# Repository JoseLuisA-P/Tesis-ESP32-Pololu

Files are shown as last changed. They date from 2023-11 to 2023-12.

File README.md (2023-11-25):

# Desarrollo de una placa de expansión para los agentes Pololu 3Pi+ que expanda sus capacidades dentro del ecosistema Robotat.

Este trabajo se desarrolló con el objetivo de ampliar las capacidades de los agentes 3Pi+ utilizados en la plataforma de pruebas Robotat. Para aumentar las capacidades del agente, se implementó un manipulador serial de 3 grados de libertad, el cual utiliza servomotores como actuadores y contiene un efector final tipo garra. También, se implementó una cámara OpenMV Cam H7 que permite capturar desde el punto del agente un fotograma o una serie de fotogramas, para realizar un livestream del agente mientras realiza otras rutinas o capturar una imagen en un punto clave de la ejecución de una rutina. Por último, se implementó un algoritmo para el estacionamiento automático del agente, el cual permite el retorno del agente a una posición establecida mientras evita los obstáculos en la plataforma, lo que permite automatizar el proceso de pruebas y asegurar un correcto funcionamiento del agente. Estas expansiones y el agente son controlados desde un TinyS3, el cual dota al agente y sus módulos con la capacidad de ser controlado por medio de una conexión WiFi, desde un cliente remoto con la capacidad de expandirse a múltiples lenguajes al utilizar instrucciones sencillas para su control.

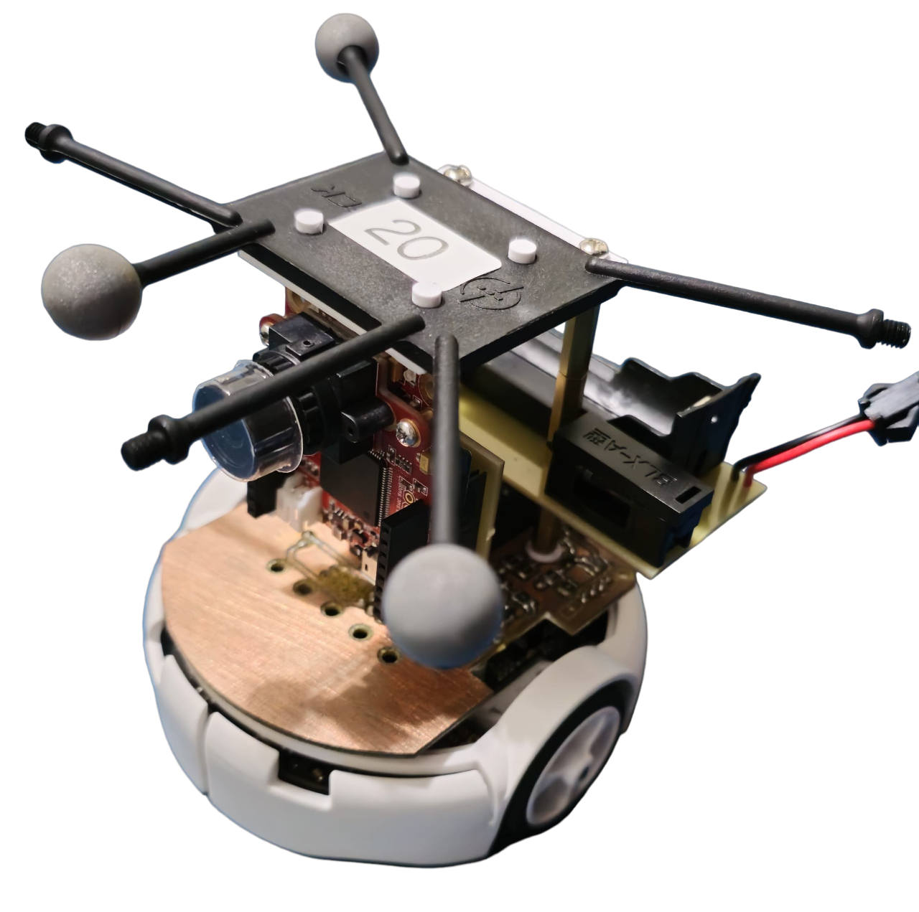
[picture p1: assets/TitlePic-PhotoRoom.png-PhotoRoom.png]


Que contiene este repositorio:
- El firmware utilizado por la placa TinyS3.
- Los códigos para el control del agente y módulos desde Python.
- Manual para el ensamble de las placas de expansion y los modulos.
- Videos de las pruebas para el correcto ensamblaje del agente.
- Enlaces a las pruebas y validación del agente.

### Tabla de contenido:
- [Plataforma de trabajo](#Plataforma-de-trabajo)
- [Estructura del repositorio](#Estructura-del-repositorio)
- [Como ensamblar los modulos y placas](#Como-ensamblar-los-modulos-y-placas)
- [Resultados](#Resultados)

### Plataforma de trabajo

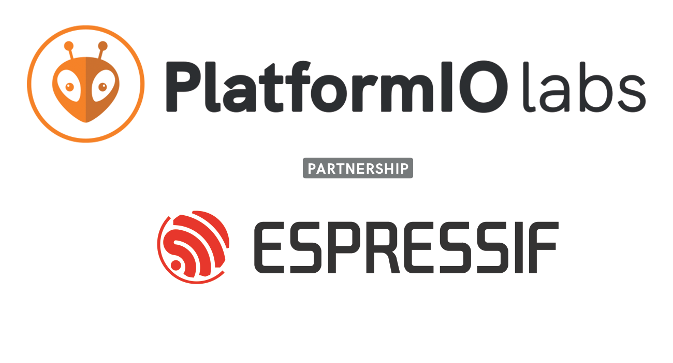
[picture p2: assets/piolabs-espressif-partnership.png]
Platformio y ESPRESSIF


El firmware del agente se desarrolló utilizando la plataforma PlatformIO en VSCode, junto con el framework de ESP-IDF desarrollado como una extensión por ESPRESSIF. La elección de VSCode para este proyecto se debe a su alta flexibilidad para configurar el entorno de desarrollo, desde las alertas visuales hasta el manejo de errores y las diversas extensiones para interactuar con módulos y bibliotecas. Además, su fácil integración con GitHub y la gestión de versiones permitieron un desarrollo más eficiente.

Se utilizó la extensión de PlatformIO debido a las diversas herramientas que contiene para programar y preparar los entornos de trabajo para diversas placas y microcontroladores. Esta extensión permite crear proyectos específicos para cada placa, configurar sus características de manera sencilla, seleccionar las versiones del lenguaje a utilizar y manejar los errores de compilación. En el lado físico, permite programar las placas desde VSCode, utilizar el monitor serial para leer los mensajes de error y configurar acorde al puerto y velocidad de comunicación con la placa. Además, facilita compilar el proyecto y verificar los errores al cargar datos a las placas.

El framework de ESP-IDF se eligió principalmente por la fácil integración de FreeRTOS, lo que permite aprovechar al máximo las capacidades de la placa y optimizar su rendimiento multitarea. Además, este framework permite utilizar las bibliotecas desarrolladas por ESPRESSIF para un manejo eficiente de los módulos de las placas basadas en ESP32, proporcionando mayor flexibilidad en su configuración y permitiendo el uso del multiplexado de los pines para los distintos módulos.

Altium Designer

Para el desarrollo de las PCBs, se utilizó Altium Designer 2021. Aunque este software permite el uso de librerías de objetos comunes, fue necesario agregar librerías personalizadas para cada uno de los componentes adquiridos localmente sin un modelo definido. La elección de Altium Designer se debe a la variedad de herramientas que ofrece para el desarrollo de PCBs y la facilidad para modificar e interconectar proyectos.

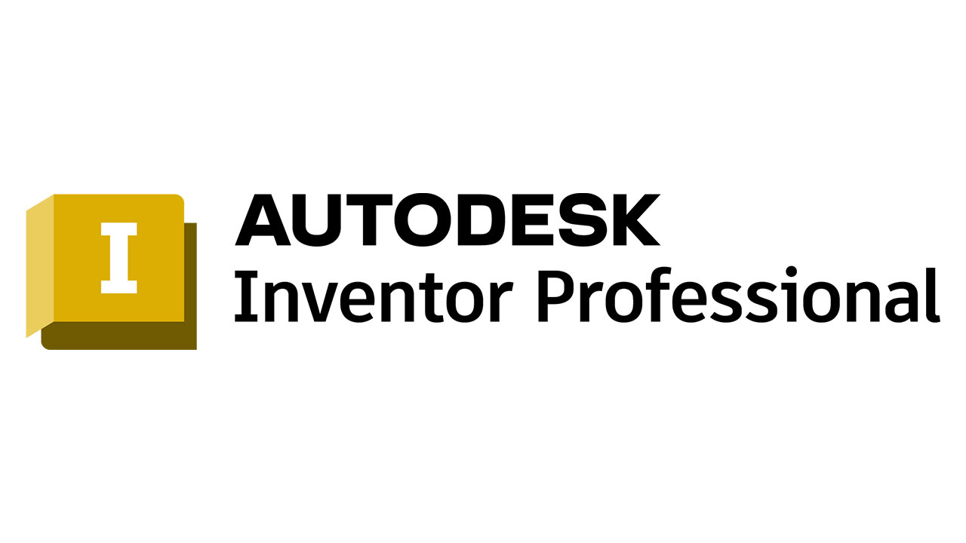
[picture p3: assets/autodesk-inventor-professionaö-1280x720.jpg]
Inventor


En cuanto al diseño de elementos físicos, se llevó a cabo en Autodesk Inventor 2024. Al contar con una interfaz robusta e intuitiva para el diseño y aprovechando la licencia profesional proporcionada por la universidad, es una herramienta que he utilizado a lo largo de mi carrera. Esta elección permitió minimizar el tiempo de desarrollo gracias a la familiaridad con la herramienta.

### Estructura del repositorio

El repositorio se encuentra estructurado de la siguiente forma:
- En la carpeta [**PruebasCOMS**](/PruebasCOMS), se encuentra el proyecto utilizado para configurar y crear el firmware del TinyS3.
- En la carpeta [**assets**](/assets) se encuentran las imágenes utilizadas para este repositorio.
- En la carpeta [**Videos**](/Videos) se encuentran videos de las pruebas de ensamblaje de este trabajo.
- En la carpeta [**Manufactura**](/Manufactura) se encuentran los archivos para manufacturar las PCBs e imprimir las piezas de este trabajo.
- En la carpeta [**ControlCliente**](/ControlCliente) se encuentran los scripts para el control del agente desde Python.
- En la carpeta [**Camara**](/Camara) se encuentra el script para el envio bajo demanda de la imagen desde la OpenMV Cam H7.

### Como ensamblar los modulos y placas

Para ensamblar los módulos y placas utilizados en este trabajo, puede hacer referencia al documento **"ManualDeEnsamble.pdf"**. En este documento, encontrará una breve descripción de las placas, así como instrucciones detalladas sobre cómo ensamblar las placas y módulos. Además, se proporciona información sobre cómo montarlos y detalles sobre otros materiales adicionales que podrían ser necesarios en el proceso.

En el proceso de ensamblaje, se incluyen referencias a pruebas creadas para observar el correcto funcionamiento del agente antes de desplegarlo, lo que facilita el diagnóstico durante su ensamblaje.

### Resultados

En este archivo se incluye un listado de enlaces a videos de YouTube sin listar, en estos se puede observar el comportamiento del agente y las diversas pruebas realizadas. Las pruebas realizadas incluyen tanto los modulos de manera individual como la integracion de los multiples modulos operando al mismo tiempo.

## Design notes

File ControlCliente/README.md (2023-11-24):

## Tabla de contenido:
- [Contenido de esta carpeta](#Contenido)
- [Requerimientos del sistema](#Sistema)
- [Clase para controlar el agente](#funciones)
- [Compatibilidad con otros lenguajes](#Compatibilidad)

## Contenido de esta carpeta

En esta carpeta se encuentra un conjunto de scripts creados para controlar el agente mediante una conexión WiFi.

En el archivo "FuncionesControlPololu.py", se ha creado la clase **PololuAgent**. Esta clase permite controlar al agente de manera sencilla mediante métodos que modifican las variables de control del agente y le hacen interactuar con su entorno.

Los archivos que comienzan con "Test_" en su nombre son pruebas realizadas para explorar las capacidades del agente, su tiempo de respuesta y la repetibilidad de sus instrucciones.

Los archivos que comienzan con "Script_" son referenciados en el manual de ensamble y sirven para realizar pruebas durante el ensamble del agente.

Por último, los archivos que comienzan con "Rutina_" se utilizan para inicializar o probar una configuración en el agente, colocándolo en posiciones iniciales o condiciones de prueba requeridas en su ensamble.

## Requerimientos del sistema

Se requiere de un sistema operativo con Python 3.x y con capacidad de conectarse por WiFi.

## Clase para controlar el agente

La clase para controlar el agente se encuentra en el script "FuncionesControlPololu.py". Esta clase permite controlar al agente y sus módulos de manera simple, sin limitar la profundidad de su control, ya que a los módulos se les pueden enviar valores en bruto para su control.

Para crear el objeto, se requiere la dirección IP del host, en este caso, la dirección de la placa al conectarse, y el puerto que se utilizará para la conexión. Al crear el objeto, se asignan en atributos privados la dirección IP, el puerto utilizado, se crea un buffer interno para el manejo de mensajes, y se crean las variables de odometría y de la batería del agente.

### Descripcion de los metodos
- `connect()`: Crea la conexión con el agente y el socket TCP a utilizar.
- `disconnect()`: Se desconecta del agente, elimina el socket creado y, si es necesario, limpia el buffer.
- `on()`: Envía el carácter de control para encender al agente y sus módulos, además, enciende la bandera para la adquisición de imágenes desde la cámara.
- `off()`: Envía el carácter de control para apagar al agente y sus módulos, y apaga la bandera para la adquisición de imágenes desde la cámara.
- `arm_raw_config()`: Envía el carácter de control para indicar al agente que debe actualizar la configuración del manipulador serial. Junto con el carácter, se envían en grados las configuraciones de las juntas del manipulador.
- `arm_coords()`: Envía el carácter de control para indicar al agente que debe actualizar el manipulador a una coordenada solicitada. Junto con el carácter de control, se envían las coordenadas para posicionar el efector final del manipulador.
- `battery_update()`: Envía el carácter de control para solicitar el nivel de la batería, recibe el dato en bruto obtenido por el ADC del TinyS3 y luego actualiza los atributos privados del voltaje y porcentaje de batería.
- `get_battery_voltage()` y `get_battery_level()`: Retornan como flotante el valor de voltaje o porcentaje de batería obtenidos.
- `set_motor_speed()`: Recibe los valores de velocidad de las ruedas izquierda y derecha como flotantes, los agrega al buffer interno del objeto junto con el carácter de control para indicar que las velocidades se deben actualizar y los envía al agente como un arreglo de bytes.
- `get_image()`: Envía el carácter de control al agente para solicitar la imagen y recibe 4800 bytes que representan el último fotograma guardado por el agente. Los agrega a un arreglo de NumPy y retorna este arreglo.
- `get_odo()`: Envía el carácter de control al agente para la solicitud de la odometría interna y recibe 12 bytes. Luego, convierte estos bytes en flotantes y los agrega a las variables internas del agente.

### Como utilizar esta clase

Previo a utilizar estos scripts es necesario conectarse a la red wifi del agente, 

**Importando la libreria y creando el objeto**
```python
from FuncionesControlPololu import PololuAgent

HOST = "192.168.4.1" #Direccion IP del host, TinyS3
PORT = 3333 #El puerto que se le va asignar al agente

agent1 = PololuAgent(HOST,PORT) #Creando el objeto con las variables
```

Para importar la librería al script que se está modificando en el momento, basta con tener el script "FuncionesControlPololu.py" en la misma carpeta e importar "PololuAgent". Con esta clase importada, se establece la dirección IP para conectarse con el agente y se asigna el puerto deseado, en este caso, se utilizó 3333 por conveniencia. Al establecer la dirección y el puerto, se puede crear el objeto pasando estas variables.

**Como conectarse y encender el agente**
```python
agent1.connect()    #Conectarse al agente
agent1.on()         #Encender al agente y sus módulos.
time.sleep(5)       #Este delay es de seguridad, asegura que todos los sistema se inicialicen correctamente
```

Con el objeto creado, se puede utilizar **connect()** para realizar la conexión con el socket. En caso de fallar la conexión, el manejo de errores al crear el socket detiene la ejecución del código e indica en la terminal el motivo por el cual no se pudo realizar la conexión. Al estar conectado al agente, se puede encender junto con sus módulos con **on()** y luego esperar de 5 a 10 segundos. Este delay es por seguridad y permite que tanto el agente, como la cámara y el manipulador serial terminen de configurarse.

**Como apagar al agente y desconectarse**
```python
agent1.off()            #Apagar al agente y sus módulos.
agent1.disconnect()     #Desconectarse del agente
```

Al terminar la ejecucion del programa se puede apagar al agente con **off()**, esto apaga al agente y sus modulos, luego se puede desconectar con **disconnect()**, lo que libera el socket del agente y permite que este acepta otra conexion a futuro. Previo a apagar el agente se recomienda dejarlo en reposo, velocidades de 0, y el manipulador serial en la posicion de reposo presentada en el manual, esto para asegurar que al encerse no se mueva de manera descontrolada o se arruine el manipulador.

***Las siguientes aplicaciones requieren al agente estar encendido y al cliente conectado a la red***

**Como mover al agente actualizando los valores de velocidades de sus llantas**

```python
#Establecer las velocidades para las llantas
velocidad_izquierda = 10.0
velocidad_derecha = 10.0

agent1.set_motor_speed(velocidad_izquierda,velocidad_derecha) #Enviar estas velocidades al agente para actualizarlas
```

Si se busca mover el agente, se puede enviar directamente la velocidad de cada llanta de manera individual. Para ello, basta con establecer su valor como flotante y luego, con **set_motor_speed()**, colocar estas velocidades. Esto enviará las velocidades al agente y actualizará su valor. Estas velocidades también pueden ser calculadas por un algoritmo de control, como un PID, y luego, pasar el resultado de la iteración al método para actualizar al agente.

**Como mover el manipulador serial**
```python
#Configuracion en grados de cada una de las juntas del manipulador
junta_1 = 90
junta_2 = 90
efector = 180

#Pasar estos valores al metodo para actualizar la configuracion en el agente
agent1.arm_raw_config(junta_1,junta_2,efector)
```

Para mover el manipulador con mayor precisión o después de utilizar un algoritmo de cinemática inversa, se puede utilizar **arm_raw_config()**. Este método recibe la configuración de cada junta en grados y la envía al agente para actualizar físicamente el manipulador.

```python
#Coordenadas para mover el efector final
coordenadaX = 50
coordenadaY = 50

#Enviar las coordenadas para posicionar el manipulador
agent1.arm_coords(coordenadaX,coordenadaY)
```

Para mover el efector final del manipulador a una posición coordenada específica, se utiliza **arm_coords()**. Este método recibe las coordenadas para mover el efector y actualiza su configuración internamente.

**Obtener la informacion de la celda**

```python
agent1.battery_update() #actualiza el valor de la bateria al ultimo leido por el agente

print(agent1.get_battery_voltage())     #Imprime el voltaje de la bateria
print(agent1.get_battery_level())       #Imprime el porcentaje restante de carga de la bateria
```

Si se requiere saber el nivel de batería del agente, primero se deben actualizar los atributos del objeto con **battery_update()**. Este método solicita al agente el último valor leído de la celda y lo envía al cliente. Con este valor actualizado, se puede obtener el voltaje de la celda con **get_battery_voltage()** o el porcentaje de carga restante con **get_battery_level()**. Al retornar un valor los últimos dos métodos, se pueden utilizar para actualizar una variable de control.

**Obtener informacion de la odometria interna del agente**

```python
agent1.get_odo()        #Obtener la odometria del agente
agent1.odoX             #Acceder a la coordenada X de la odometria
agent1.odoY             #Acceder a la coordenada Y de la odometria
agent1.odoTheta         #Acceder al ángulo Theta de la odometria
```

Para obtener la configuración del agente por medio de odometría interna, se puede utilizar **get_odo()**. Este método solicita el valor actualizado de odometría del agente y lo envía al cliente. Al haber actualizado la odometría del agente en el objeto, se puede acceder a sus valores utilizando **.odoX**, **.odoY** o **.odoTheta**. Las coordenadas están en metros y el ángulo está en radianes.

**Obtener el ultimo fotograma desde el agente y graficarlo con Matplolib**
```python
raw_image = agent1.get_image()                  #Obtener el fotograma como un vector fila de bytes
processed_image = raw_image.reshape(60,80)      #Cambiar sus dimensiones por una matriz de 60X80
fg = plt.figure()                               #Crear la figura
ax = fg.gca()                                   #Crear el objeto para los ejes
fg.show()                                       #Mostrar la figura
h = ax.imshow(processed_image, cmap = 'gray')   #Actualizar el valor de la figura con el arreglo y colocarlo en blanco y negro
plt.show()                                      #Mostrar la imagen
```

Para obtener el último fotograma obtenido con la cámara, se puede utilizar **get_image()**. Este método solicitará al agente el último fotograma obtenido y lo enviará al cliente como un vector fila de bytes. Luego, con este valor en bruto, se puede redimensionar con NumPy, crear una figura y graficarlo con Matplotlib para visualizar lo que ve el agente.

```python
#Se utiliza para temporizar la toma de fotogramas
actual_time = time.time()
n = 0
capture = 0

#Durante 20 segundos se toma video de lo que ve el agente y se imprime en pantalla
while(n < 200):
    elapsed_time = time.time()
    diff = elapsed_time - actual_time
    
    if(elapsed_time > 0.1):
        capture = 1
        n = n + 1
        
    if(capture):
        raw_image = agent1.get_image()
        if(len(raw_image) >= 4700):
            processed_image = raw_image.reshape(60,80)
            h.set_data(processed_image)
            draw(), pause(0.05)
            capture = 0
        else:
            agent1.disconnect()
            time.sleep(0.1)
            agent1.connect()
            
plt.close()
```

En caso se requiera hacer un stream de la imagen desde el agente, se puede emplear el código previo. Este solicita la imagen y al recibir correctamente el fotograma, actualiza la imagen a una tasa de 10 FPS. En caso de fallar, se desconecta del agente para limpiar el buffer y luego solicitar de nuevo la imagen.

***Si se necesita utilizar multiples acciones del agente en conjunto, en los scripts incluidos en esta carpeta se pueden ver multiples ejemplos***

## Compatibilidad con otros lenguajes

Dado que esta clase se escribió utilizando la menor cantidad de librerías en Python, utiliza estructuras para la conversión entre bytes y tipos de datos, y utiliza sockets para conectarse con el agente. Virtualmente, se puede migrar a otros lenguajes que tengan estas funcionalidades con baja dificultad, siempre conservando la baja latencia.

Entre los lenguajes recomendados para su migración están:
- Matlab
- Java
- C++

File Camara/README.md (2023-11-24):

El script presentado en esta carpeta contiene la configuración requerida para el envío bajo demanda de los fotogramas capturados por la cámara. La configuración de la cámara y resolución se pueden modificar acorde a los requerimientos del proyecto para procesar la información necesaria. Se pueden agregar más eventos en el bucle while para que la cámara sea capaz de procesar datos, disminuir la carga en el agente, o realizar un análisis de la imagen y enviar los datos.

Para poder enviar los datos, se debe utilizar la siguiente estructura:

```python
if(handshake.value() == 0):
    envio = sensor.snapshot()
    cs_pin.low()
    interface.send(envio)
    cs_pin.high()
```

En esta condición if, se envía el fotograma al agente. Para que esto suceda, el fotograma debe estar en blanco y negro con una resolución de 60x80 bytes. Si se desea enviar otros datos por SPI desde la cámara, se puede modificar este bucle if y enviar la estructura de datos requerida. Sin embargo, esto requiere modificar la función **AskForPicture()** en el firmware del TinyS3 para que reciba el mensaje del tamaño solicitado y lo procese acorde a lo requerido.

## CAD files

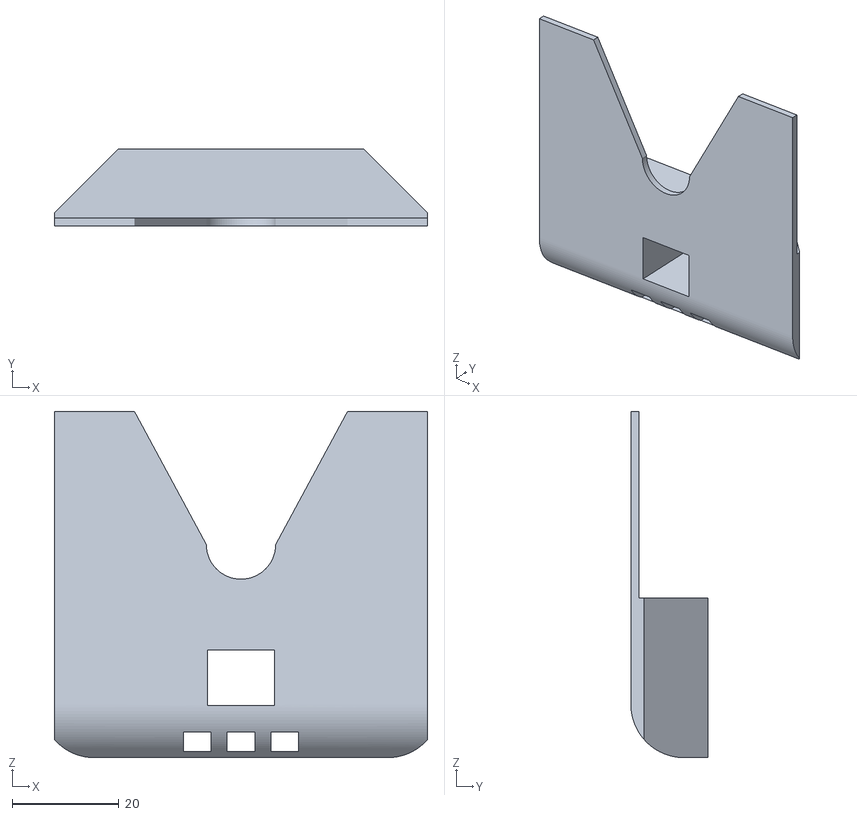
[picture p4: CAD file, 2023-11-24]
Manufactura/Estacion de carga/CharginStationV2.stl
70.0 x 14.5 x 65.0

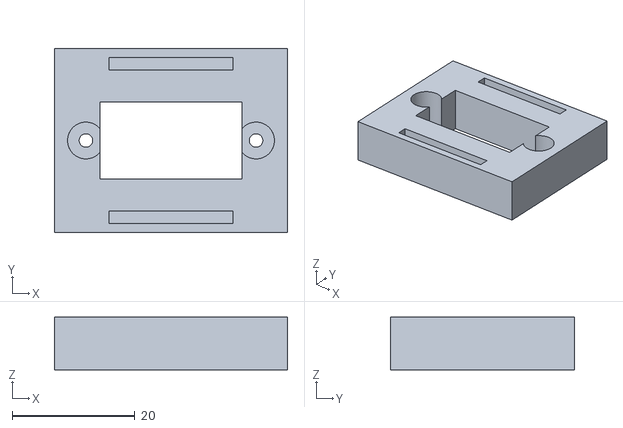
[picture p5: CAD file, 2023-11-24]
Manufactura/Manipulador Serial/BaseGarra-02.stl
38.0 x 30.0 x 8.60

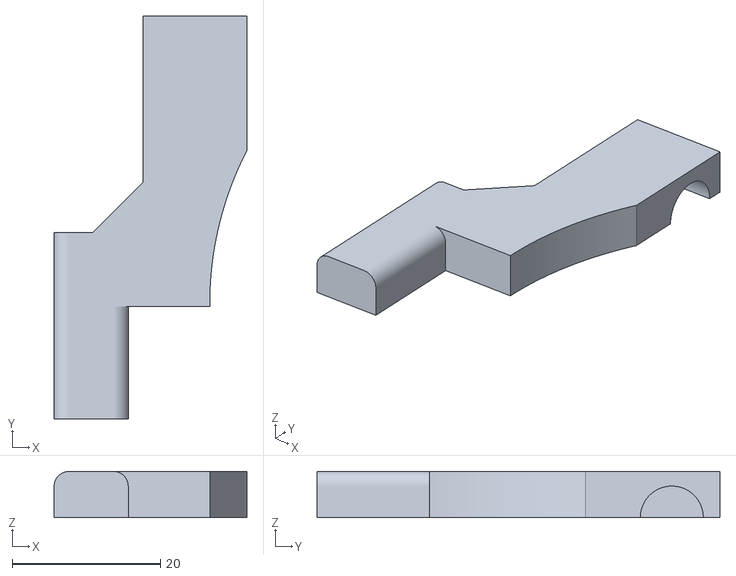
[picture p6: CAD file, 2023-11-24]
Manufactura/Estacion de carga/SoporteCableV2.stl
26.0 x 54.4 x 6.22

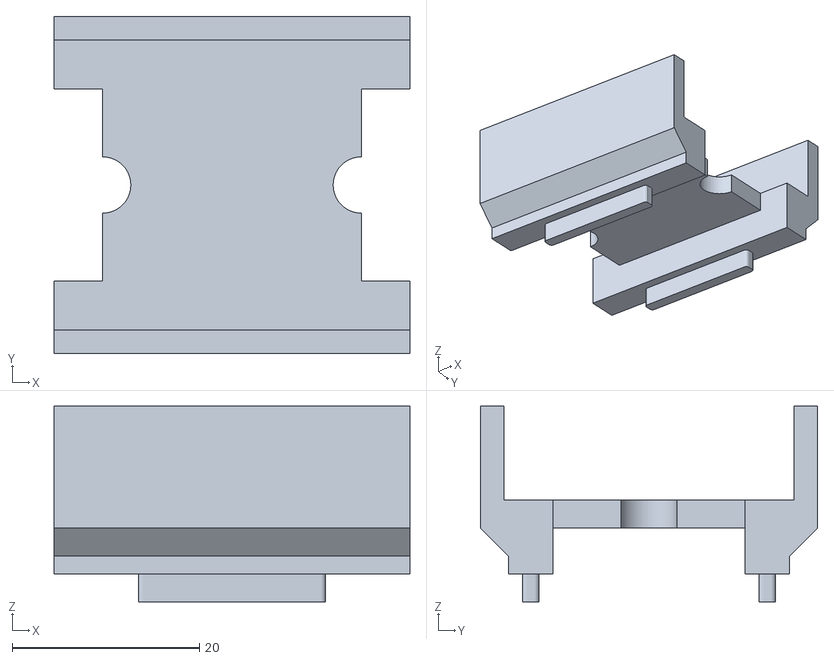
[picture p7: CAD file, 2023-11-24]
Manufactura/Manipulador Serial/BaseGarra-01.stl
38.0 x 36.0 x 20.9

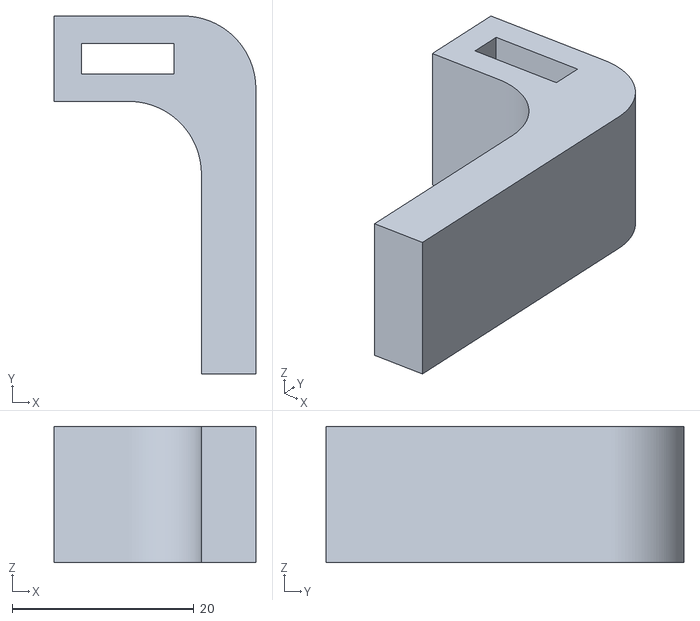
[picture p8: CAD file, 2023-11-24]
Manufactura/Estacion de carga/HolderBarraHubX4.stl
22.2 x 39.4 x 15.0

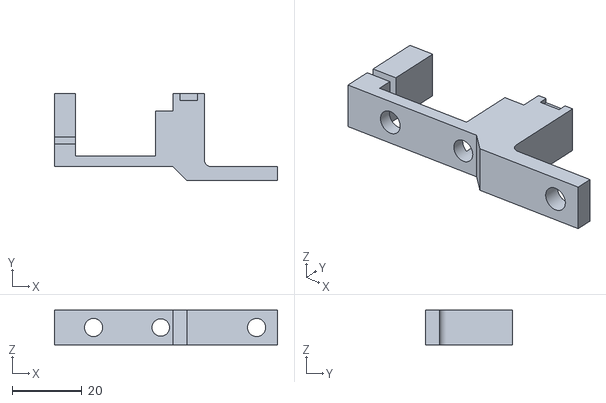
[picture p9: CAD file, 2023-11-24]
Manufactura/Manipulador Serial/Eslabon1-02.stl
64.0 x 25.0 x 10.0

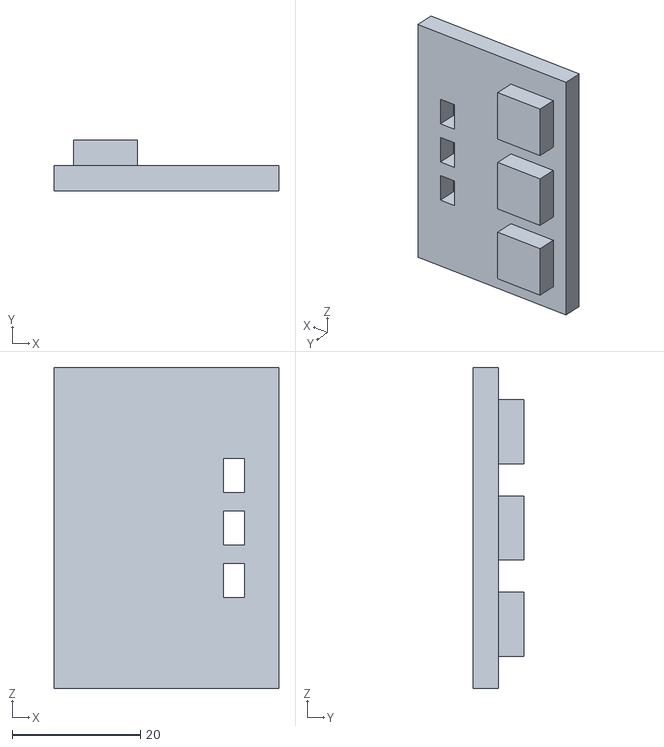
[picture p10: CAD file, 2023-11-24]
Manufactura/Estacion de carga/HolderChargerX3.stl
35.0 x 8.00 x 50.0

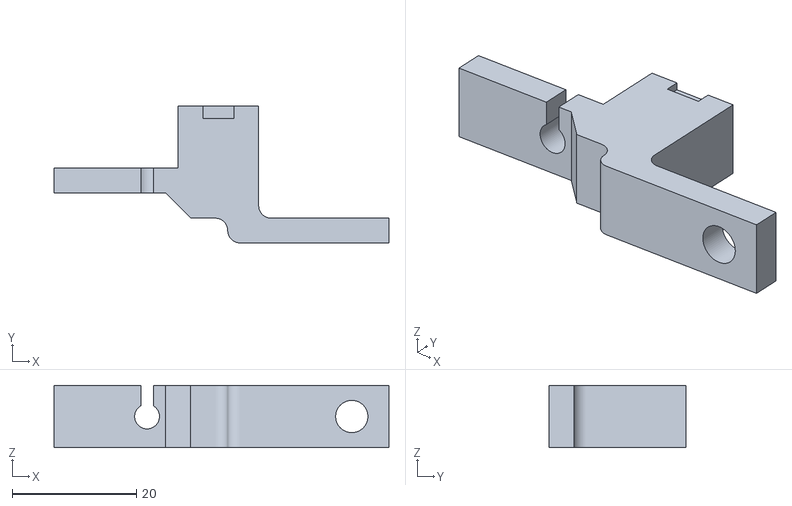
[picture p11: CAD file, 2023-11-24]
Manufactura/Manipulador Serial/Eslabon2-02.stl
54.0 x 22.1 x 10.0

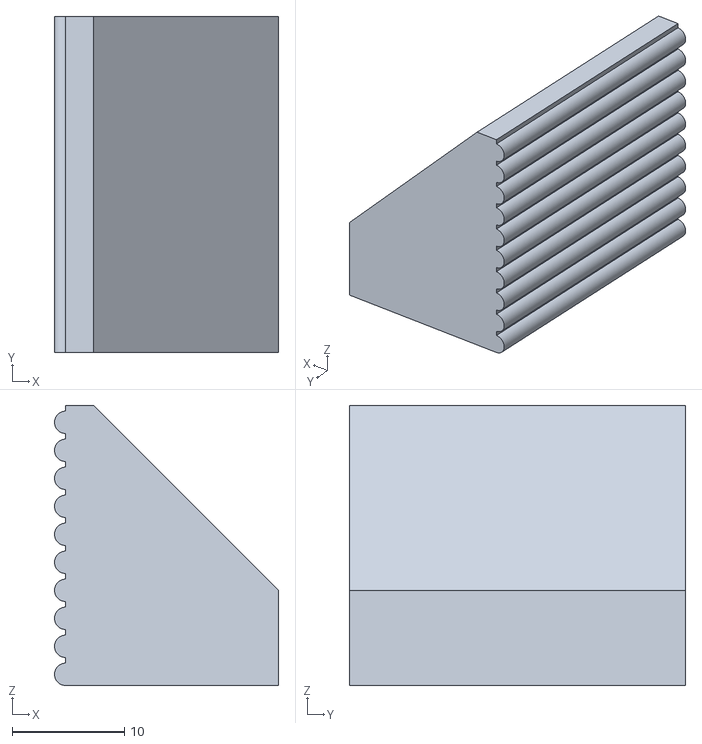
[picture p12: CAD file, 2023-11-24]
Manufactura/Manipulador Serial/GarraManoX2.stl
20.0 x 30.0 x 25.0

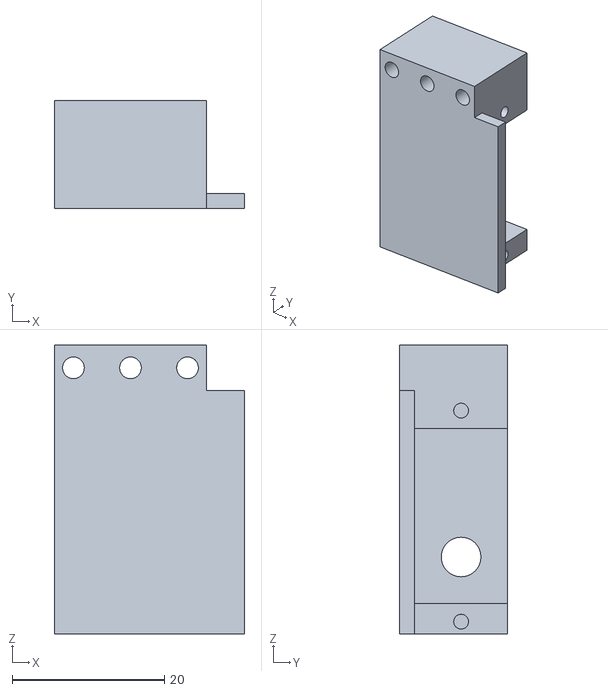
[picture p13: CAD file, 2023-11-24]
Manufactura/Manipulador Serial/BaseBrazoV1.stl
25.0 x 14.2 x 38.0

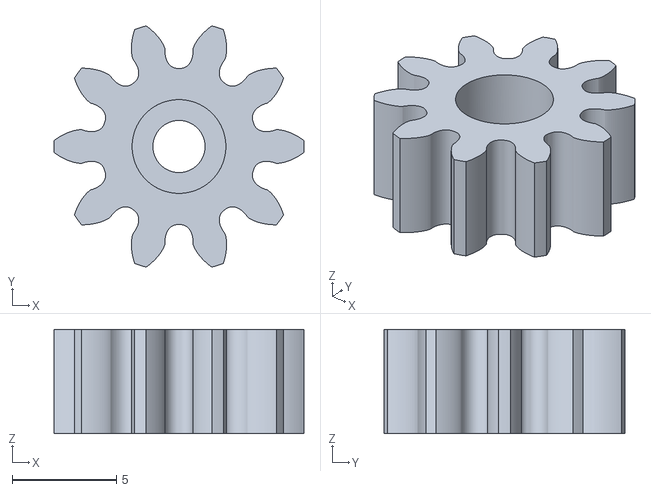
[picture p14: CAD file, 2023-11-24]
Manufactura/Manipulador Serial/EngraneServoX2.stl
12.0 x 11.6 x 5.00

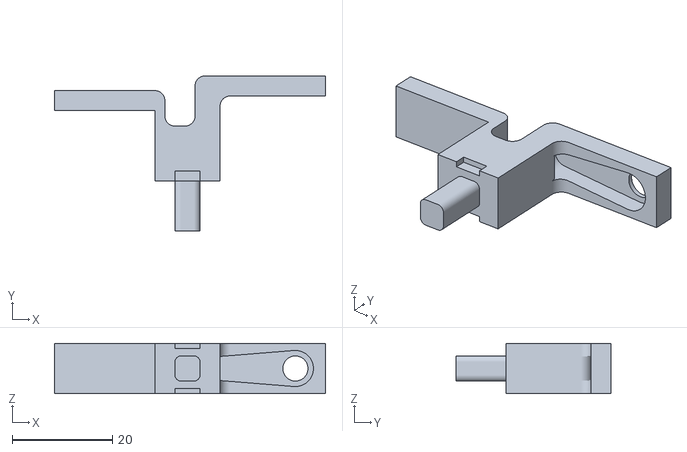
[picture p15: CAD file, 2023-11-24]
Manufactura/Manipulador Serial/Eslabon2-01.stl
54.0 x 30.9 x 10.0

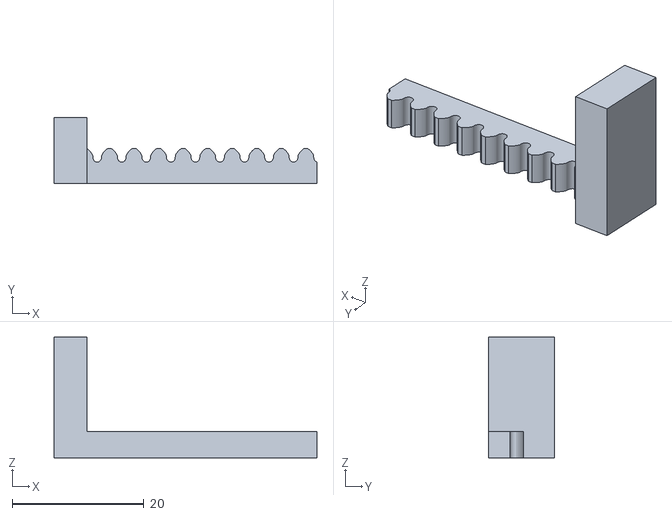
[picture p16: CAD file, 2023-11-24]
Manufactura/Manipulador Serial/BrazoGarraX2.stl
40.0 x 10.0 x 18.4

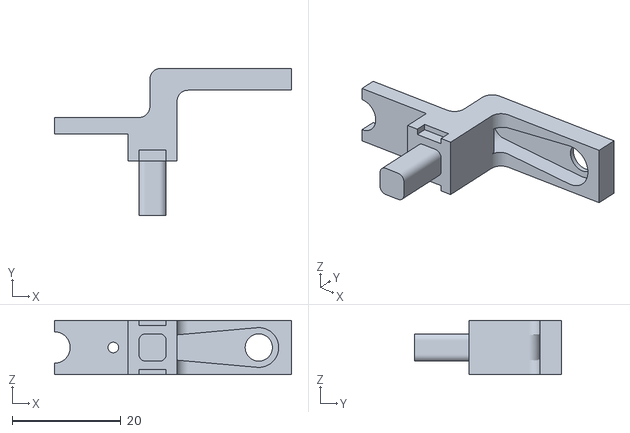
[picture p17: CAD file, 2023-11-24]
Manufactura/Manipulador Serial/Eslabon1-01.stl
43.5 x 27.0 x 10.0

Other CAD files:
Manufactura/Estacion de carga/SoporteCableV2P2.stl

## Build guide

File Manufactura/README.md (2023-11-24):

# En cada carpeta se encuentran los archivos STL o planos de corte para fabricar las piezas del agente. 
## Estos están listos para ser enviados al MakerLab y así proceder con la manufactura.

En algunos de los archivos STL adjuntos, al final de su nombre, se encuentra un sufijo "XN", donde N es la cantidad de piezas a imprimir. Esta cantidad corresponde a generar una instancia del modelo para ensamblar un componente completo. Además, sigue la nomenclatura del MakerLab para asegurar que se generen los elementos adecuados. 
En esta carpeta no se incluyen los archivos de documentación de las piezas, que indican el orden de impresión, dimensiones o cantidad a imprimir, ya que esta información puede variar sin previo aviso por parte del MakerLab.

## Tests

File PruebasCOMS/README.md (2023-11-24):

## Tabla de contenido:
- [Acerca de este proyecto](#Acerca-de-este-proyecto)
- [Requerimientos del proyecto](#Requerimientos-del-proyecto)
- [Preparando el entorno](#Preparando-el-entorno)
- [Configuracion de la placa](#Configuracion-de-la-placa)
- [Breve descripcion de las funciones](#Breve-descripcion-de-las-funciones)

## Acerca de este proyecto
Este proyecto se creó para el desarrollo del firmware a utilizar en el TinyS3, el cual es el módulo central de control del agente robótico. Este dota al agente de la capacidad de comunicarse con clientes a través de WiFi, utilizando una lógica simple para el envío y recepción de datos. Además, esta placa permite controlar los módulos del manipulador serial y la cámara montada en el agente, tanto de manera individual como en paralelo, al fijar el envío de instrucciones en un orden específico que se presenta posteriormente.

Se desarrolló con el framework de ESP-IDF para el uso de las librerías creadas por ESPRESSIF para las placas basadas en el chip ESP32. Además, se utilizó para integrar FreeRTOS en el proyecto y mejorar el rendimiento del agente en actividades multitarea.

En este contexto, FreeRTOS dota al agente con un pseudo sistema operativo, el cual permite al agente responder a instrucciones enviadas desde un cliente, actualizar sus variables de control y actualizar el estado de sus módulos, con muy baja latencia. Esto es ideal para agentes robóticos en plataformas de desarrollo y estudio, ya que amplía la posibilidad de implementarlo en algoritmos de enjambre.

## Requerimientos del proyecto

Este proyecto puede ser modificado en Windows, MacOS o cualquier distribución de Linux capaz de ejecutar VSCode y PlatformIO. Además, el equipo debe ser capaz de ejecutar Python 3.x y Matlab R2021a en adelante. Estos requisitos son necesarios para poder ejecutar las funciones del cliente, interactuar con el robotat y tener la capacidad de modificar el proyecto.

## Preparando el entorno

Para instalar VSCode, se puede seguir el siguiente [enlace](https://code.visualstudio.com/docs/setup/setup-overview). Este enlace proporciona una visión general de VSCode, y se debe de seleccionar el sistema operativo que se esta utilizando. Se recomienda tener GitHub instalado e integrarlo en el entorno de VSCode, lo que facilitará, en el futuro, la actualización de la información del proyecto al contar con un punto de retorno seguro y comprobado, ademas de un eficiente manejo de versiones.

Una vez que se ha instalado VSCode en el sistema, es necesario instalar la extensión de PlatformIO, lo cual se puede realizar siguiendo las instrucciones del siguiente [enlace](https://platformio.org/install/ide?install=vscode).

Con la extensión de PlatformIO instalada, se debe de descargar este proyecto en su última versión para modificarlo, realizar un fork o clonarlo en un repositorio personal. Teniendo el proyecto disponible en tu equipo, puedes importarlo haciendo clic en **Open project** o **Abrir proyecto** en la página de inicio de PlatformIO.

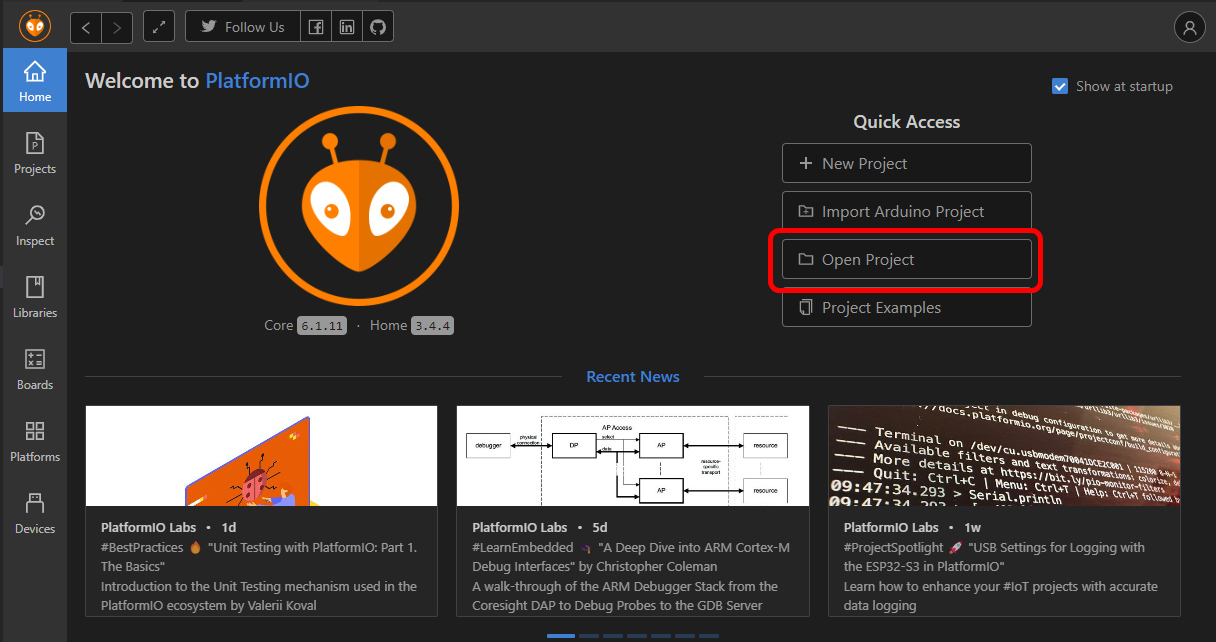
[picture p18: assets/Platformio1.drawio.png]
Importar el proyecto


Al hacer clic en este acceso rápido, se selecciona la carpeta donde se descargó el proyecto y, luego, se debe de hacer clic en abrir. Este proceso descargará las librerías requeridas por el proyecto, actualizará las librerías existentes y descargará los scripts necesarios para programar la placa. Este proceso suele tomar entre 5 y 25 minutos, y es importante que la computadora no entre en reposo durante este tiempo. Sin embargo, no es necesario mantener la aplicación abierta, por lo que se puede realizar otras actividades mientras se importa el proyecto.

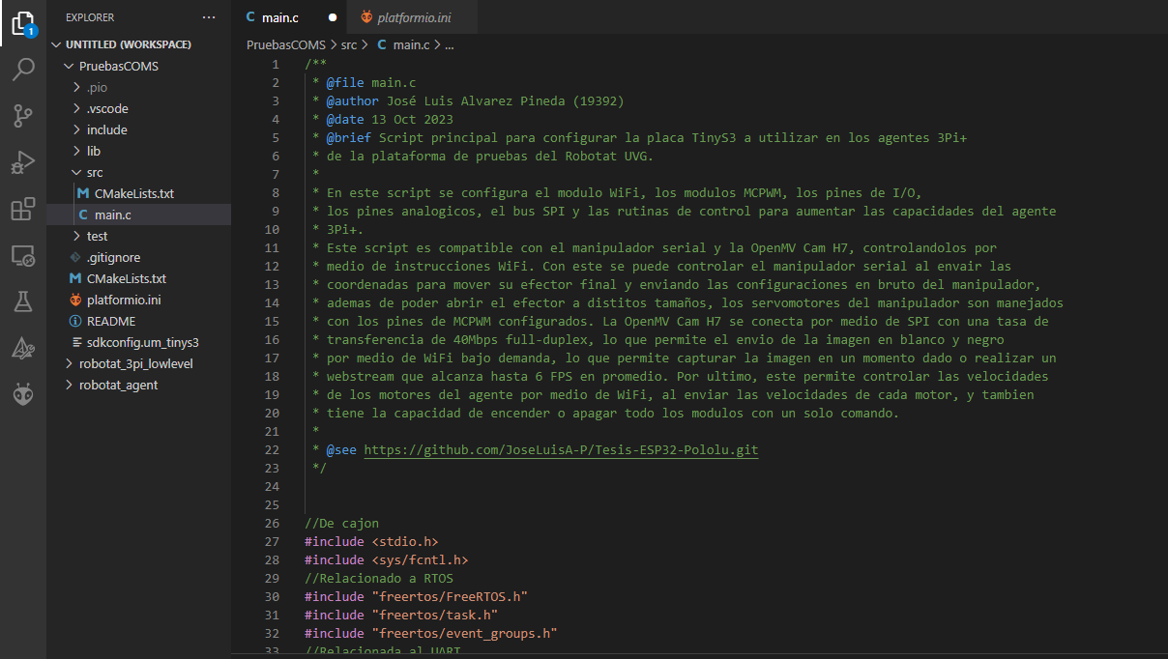
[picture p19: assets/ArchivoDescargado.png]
Como se ve el proyecto importado


Al finalizar la importación del proyecto, se agregará al workspace actualmente abierto o a un workspace sin nombre, como se muestra a la izquierda. Dentro de él, en la carpeta "src", encontrarás el archivo principal (main.c) del proyecto. Al abrirlo, verás la pantalla como se muestra en la imagen superior. Después de dar clic en compilar, se generará una versión lista para cargar en la placa y comenzar a trabajar. Con esto completado, el proyecto se ha importado correctamente y está listo para ser modificado.

En caso de que surjan errores durante la compilación o la importación, las advertencias de PlatformIO son explícitas y permiten resolver los errores al leerlos de manera adecuada. Si, después de seguir las indicaciones de PlatformIO, no puedes importar el proyecto, se recomienda descargarlo e instalarlo en el escritorio de tu equipo.

## Configuracion de la placa

Para configurar la placa al iniciar un proyecto nuevo o importar porciones del proyecto, se puede utilizar la siguiente configuración:

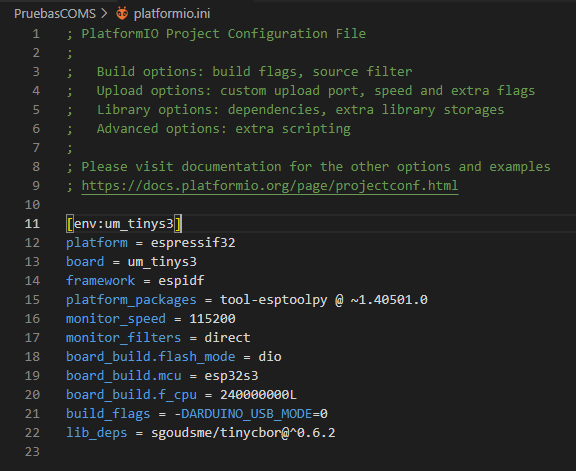
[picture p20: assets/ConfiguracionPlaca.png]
Configuraion de la placa


La configuración presentada es capaz de ejecutar todas las librerías utilizadas y aprovechar al máximo las capacidades de la placa. Además, permite la lectura de distintos tipos de mensajes de la placa y los diferencia por color, haciendo más intuitivo el proceso de pruebas y desarrollo.

# Breve descripcion de las funciones
Las funciones utilizadas para configurar este proyecto se pueden separar en grupos, cada uno encargado de configurar un módulo y agregar propiedades para realizar tareas específicas.

**Configuración del Módulo WiFi:**
- `wifi_init_softap()`: Inicializa y configura el módulo WiFi como punto de acceso (AP).
- `nvs_init()`: Inicializa el sistema de almacenamiento no volátil y lo actualiza a la versión más actual al cargar el firmware.
- `wifi_event_handler()`: Se encarga de manejar los eventos que se llevan a cabo en la red WiFi, además, imprime los eventos para facilitar las pruebas.

**Configuración del Socket TCP:**
- `tcp_socket_init()`: Inicializa el socket TCP y crea la tarea del handler para manejar los mensajes y solicitudes del cliente.
- `handle_socket()`: Maneja los datos recibidos por el cliente y realiza acciones después de leer la variable de control.

**Comunicación con el Agente a través del Bus UART:**
- `UART_init()`: Configura el bus UART con los parámetros requeridos por el agente.
- `uart_tx()` y `uart_rx()`: Encargadas del envío y recepción periódico de datos al agente utilizando el bus UART.
- `decodeCBOR()`: Decodifica el contenedor de CBOR recibido en el bus y asigna los valores en este a las variables de odometría interna.
- `encodeCBOR()`: Codifica las velocidades de las ruedas del agente, agregándolas a un contenedor de CBOR.

**Comunicación con la Cámara a través del Bus SPI:**
- `SPI_init_config()`: Configura el módulo SPI, asigna los callbacks para las transmisiones y activa el pin de handshake.
- `my_pre_cb()` y `my_post_cb()`: Son los callbacks de la transmisión SPI y cambian el estado del pin de handshake para solicitar información a la cámara.
- `AskForPicture()`: Bucle que solicita bajo demanda la imagen desde la cámara y actualiza el buffer de la última imagen capturada.

**Manipulador Serial utilizando el Módulo MCPWM:**
- `mcpwm_initialize()`: Configura e inicializa los 3 canales de PWM.
- `updatePositionSCH()`: Actualiza los ciclos de trabajo de los canales de PWM de cada servomotor ante modificaciones realizadas por el cliente.
- `CalcConfig()`: Calcula la configuración y ciclo de trabajo requerido por los servomotores para colocarlos en una coordenada especificada por el cliente.

**Lectura de la Celda para la Alimentación del Agente:**
- `ADCConfig()`: Configura e inicializa el canal ADC en modo oneshot.
- `BatteryUpdate()`: Realiza lecturas periódicas al nivel de la batería y almacena el último valor leído en una variable.

Dado que el código utiliza envíos de datos al cliente bajo demanda y parte de estos datos son recabados de manera periódica al encender el agente, se utiliza `initSemaphores()` para inicializar y configurar las estructuras de control.

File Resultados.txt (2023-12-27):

Enlace a la lista de odometria: https://www.youtube.com/playlist?list=PLaFg6usfbdtRm5OenLyibr4apW4UIxrPD

Enlace a la lista del manipulador serial: https://www.youtube.com/playlist?list=PLaFg6usfbdtTwx68LOk1SOFYHa42CXAxg

Enlace a la lista del livestream: https://www.youtube.com/playlist?list=PLaFg6usfbdtTZ6Gpa1hlmyx4xLoYTJxLw

Enlace a la lista de odometria y livestream: https://www.youtube.com/playlist?list=PLaFg6usfbdtQjJjsxPqYbJ4kCr4Ms4ZXF

Enlace a la lista de odometria y manipulador serial: https://www.youtube.com/playlist?list=PLaFg6usfbdtSEN4Z2sSBTVOfirNpEE59O

Enlace a la lista de pruebas del manual:https://www.youtube.com/playlist?list=PLaFg6usfbdtSpVdTMnJFs3VnT3rEh2SlV

Enlace a la lista de parqueo del agente: https://www.youtube.com/playlist?list=PLaFg6usfbdtT4JosoJN846-d9nKsDRila

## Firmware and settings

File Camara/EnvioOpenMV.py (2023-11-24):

import sensor, image, pyb
from pyb import SPI

RED_LED_PIN = 1

sensor.reset()
sensor.set_pixformat(sensor.GRAYSCALE)
sensor.set_framesize(sensor.QQQVGA)

handshake = pyb.Pin('P4',pyb.Pin.IN)
pyb.LED(RED_LED_PIN).on()
sensor.skip_frames(time=1000)

interface = pyb.SPI(2, SPI.MASTER,baudrate=40*1000*1000, polarity = 0, phase = 0)
cs_pin = pyb.Pin("P3",pyb.Pin.OUT_PP) #Es necesario activar el pin manualmente

comprate = 10

#envio = sensor.snapshot().compressed(comprate).bytearray()
envio = sensor.snapshot()
print(envio.size())
#print(len(envio))

while(1):
    pyb.LED(RED_LED_PIN).off()
    if(handshake.value() == 0):
        #pyb.LED(RED_LED_PIN).on()
        #envio = sensor.snapshot().compressed(comprate).bytearray()
        envio = sensor.snapshot()
        #print(len(envio))
        cs_pin.low()
        interface.send(envio)
        cs_pin.high()
        #print("Enviado")

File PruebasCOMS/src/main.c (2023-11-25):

/**
 * @file main.c
 * @author José Luis Alvarez Pineda (19392)
 * @date 13 Oct 2023
 * @brief Script principal para configurar la placa TinyS3 a utilizar en los agentes 3Pi+
 * de la plataforma de pruebas del Robotat UVG.
 *
 * En este script se configura el modulo WiFi, los modulos MCPWM, los pines de I/O,
 * los pines analogicos, el bus SPI y las rutinas de control para aumentar las capacidades del agente
 * 3Pi+.  
 * Este script es compatible con el manipulador serial y la OpenMV Cam H7, controlandolos por 
 * medio de instrucciones WiFi. Con este se puede controlar el manipulador serial al envair las 
 * coordenadas para mover su efector final y enviando las configuraciones en bruto del manipulador,
 * ademas de poder abrir el efector a distitos tamaños, los servomotores del manipulador son manejados 
 * con los pines de MCPWM configurados. La OpenMV Cam H7 se conecta por medio de SPI con una tasa de 
 * transferencia de 40Mbps full-duplex, lo que permite el envio de la imagen en blanco y negro 
 * por medio de WiFi bajo demanda, lo que permite capturar la imagen en un momento dado o realizar un
 * webstream que alcanza hasta 6 FPS en promedio. Por ultimo, este permite controlar las velocidades
 * de los motores del agente por medio de WiFi, al enviar las velocidades de cada motor, y tambien 
 * tiene la capacidad de encender o apagar todo los modulos con un solo comando.
 * 
 * @see https://github.com/JoseLuisA-P/Tesis-ESP32-Pololu.git
 */


//De cajon
#include <stdio.h>
#include <sys/fcntl.h>
//Relacionado a RTOS
#include "freertos/FreeRTOS.h"
#include "freertos/task.h"
#include "freertos/event_groups.h"
//Relacionada al UART
#include "driver/uart.h"
#include "driver/gpio.h"
#include "sdkconfig.h"
//Relacionado al Wifi
#include "esp_mac.h"
#include "esp_wifi.h"
#include "esp_event.h"
#include "esp_log.h"
#include "nvs_flash.h"
#include "lwip/err.h"
#include "lwip/sys.h"
//Implementando el stack TCP-IP
#include "esp_system.h"
#include "esp_netif.h"
#include "lwip/sockets.h"
#include <lwip/netdb.h>
//Manejo de Strings
#include <string.h>
//Manejo de los servos
#include "driver/ledc.h"
#include "driver/mcpwm.h"
#include "soc/mcpwm_reg.h"
#include "soc/mcpwm_struct.h"
//Relacionado al SPI
#include "driver/spi_slave.h"
#include "driver/spi_master.h"
//Codificando con CBOR
#include "../src/cbor.h"
//Operaciones trigonometrica
#include <math.h>
//Lectura con el ADC
#include "esp_adc/adc_oneshot.h"
#include "esp_adc/adc_cali.h"
#include "esp_adc/adc_cali_scheme.h"

//Variables para pruebas y cambio de placa

#define isTinyS3
//#define testeo

//Parametros para la configuracion del servidor
#define SSID                "Pololu3Pi+"
#define WIFIPASSWORD        "MT30062023"
#define WIFICHANNEL         2
#define MAXCONNECTIONS      1

//Puerto para la comunicacion
#define PORT 3333
int sock;
int LisSock;
uint8_t tcpavail = 0;
uint8_t odometry_request = 0;
uint8_t battery_request = 0;

//Parametros para configurar el timer del LEDC
#define LEDC_TIMER              LEDC_TIMER_0
#define LEDC_MODE               LEDC_LOW_SPEED_MODE
#define LEDC_DUTY_RES           LEDC_TIMER_10_BIT // Resolucion del ciclo de trabajo de 13 bits

//Parametros para configurar el canal y pin del servo con el LEDC
#define SERVO1_CHANNEL          LEDC_CHANNEL_0
#define SERVO1_PIN              GPIO_NUM_1
#define SERVO2_CHANNEL          LEDC_CHANNEL_1
#define SERVO2_PIN              GPIO_NUM_2
#define SERVO3_CHANNEL          LEDC_CHANNEL_2
#define SERVO3_PIN              GPIO_NUM_3

//Parametros para calcular el duty en base al angulo
const uint32_t minDeg = 0;
const uint32_t maxDeg = 180;
const uint32_t minDuty = 500;
const uint32_t maxDuty = 1000;
uint32_t dutyValue;

//Configuracion de pines para el SPI
#define SPI_NAME    SPI2_HOST
#define SPI_MISO    GPIO_NUM_37
#define SPI_MOSI    GPIO_NUM_35
#define SPI_CLK     GPIO_NUM_36
#define SPI_CS      GPIO_NUM_34
#define SPI_HAND    GPIO_NUM_9

//PIN para encender el pololu
#define POLOLUSWITCH    GPIO_NUM_4

//Variables para las solicitudes
#define BUFFER_SIZE 4800                // Tamaño del Buffer para la recepcion de datos
char rx_buffer[BUFFER_SIZE];            // Buffer para los datos recibidos por SPI
uint8_t SPIAsk = 0;                     // Bandera de control para la solicitud de datos
spi_device_interface_config_t CamH7;    // Configuracion de la camara como dispositivo conectado por SPI
spi_device_handle_t  SPIHandle;         // Handle para el modulo SPI configurado

static const char *TAG = "Prueba"; //TAG para el log de errores o informacion

#define SERVO_MIN_PULSEWIDTH 400  // Pulso minimo en microsegundos
#define SERVO_MAX_PULSEWIDTH 2400 // Pulso maximo en microsegundos
#define SERVO_MAX_DEGREE 180      // Angulo maximo para los manipuladores

#define CBOR_BUF_SIZE       (32)    //Tamaño del mensaje de CBOR
#define CBOR_MSG_MIN_SIZE   (16)    //Tamaño minimo del mensaje de CBOR

uint8_t sendOdo = 0;                                // Para enviar la odometria al cliente
char odo_buffer[BUFFER_SIZE];                       // Buffer para la odometria
float xi_odo[3];                                    // Valores de [x,y,theta] del agente
uint8_t cbor_buf_tx[CBOR_BUF_SIZE] = {0};           // Buffer para la recepcion de datos CBOR
uint8_t cbor_buf_rx[CBOR_BUF_SIZE] = {0};           // Buffer para el envio de datos CBOR
static const unsigned int odoread_time_ms = 100;    // Tiempo de control para la lectura de la odometria
CborEncoder encoder, array_encoder;                 // Variable de encoder y de encoder para un arreglo de datos en CBOR
CborParser parser;                                  // Parser para el arreglo en CBOR
volatile float phi_ell = 0;                         // Variable para la velocidad de la rueda izquierda
volatile float phi_r = 0;                           // Variable para la velocidad de la rueda derecha

union{
    float input_flotante;
    uint8_t bytes[4];
} odoX, odoY, odoTheta; //Para convertir los floats en bytes y luego enviarlos al cliente

float odo_x = 0;                        //Guarda el ultimo valor de X leido por odometria
float odo_y = 0;                        //Guarda el ultimo valor de Y leido por odometria
float odo_theta = 0;                    //Guarda el ultimo valor de Theta leido por odometria
uint8_t odoBuffer[sizeof(float)*3];     //Buffer para la decodificacion de los datos

#define RX_BUF_SIZE         (1024)          //Tamaño maximo del buffer
#define UART_PORT           UART_NUM_2      //Modulo UART utilizado para la comunicacion
#define TXD_PIN             (GPIO_NUM_7)    //Numero de GPIO utilizado para TX
#define RXD_PIN             (GPIO_NUM_8)    //Numero de GPIO utilizado para RX

static const unsigned int control_time_ms = 100; //Tiempo de control, para la transmision de las variables de controla al agente

SemaphoreHandle_t xSemaphore1, xSemaphore2; //Estructura de control para los mensajes

/**
 * \struct
 * @brief Estuctura utilizada para conservar los parametros del manipulador serial.
 *
 * En esta estructura se incluyen los valores de configuracion de las juntas y su 
 * ciclo de trabajo.  Los valores de las juntas es el angulo que deben de mantener
 * acorde a la ultima configuracion realizada, con este valor se realizan los pasos 
 * para calcular el nuevo ciclo de trabajo y asi colocar la junta en esa configuracion,
 * ademas de utilizarse como el ultimo valor configurado.
 * El valor del ciclo de trabajo se utiliza para mantener la posicion luego de 
 * actualizar la configuracion de la junta y colocar el manipulador en su posicion
 * luego de un reinicio.
 * 
 */

typedef struct {
    uint32_t joint1;    /**< Configuracion de la junta 1, en grados. */
    uint32_t joint2;    /**< Configuracion de la junta 2, en grados. */
    uint32_t gripper;   /**< Configuracion de la junta 3, en grados. */
    uint32_t duty_us1;  /**< Ciclo de trabajo en la junta 1. */
    uint32_t duty_us2;  /**< Ciclo de trabajo en la junta 2. */
    uint32_t duty_us3;  /**< Ciclo de trabajo en la junta 3. */
}   ManSer;

ManSer brazo = {60,60,100,0,0,0}; //Inicializando los valores en la estructura

uint32_t configj1,configj2,configj3; //Configuracion en grados de las juntas para su control
uint32_t step1,step2,step3; //Para realizar los pasos en los ajustes de las juntas

uint32_t q1, q2; //Configuraciones calculadas
uint32_t es1 = 47; //Largo eslabon 1
uint32_t es2 = 68; //Largo eslabon 2 
uint8_t coordX,coordY;//Configuraciones en XY para colocar el brazo
uint8_t updateCoords = 0;//Para actualizar la configuracion luego de enviar coordenadas

//Variables para el ADC
static int adc_raw[1][10]; //Valores en bruto del ADC
adc_oneshot_unit_handle_t adc1_handle; //Handler para las interrupciones
int batlevel = 0; //Flag para cuando se lee el nivel de bateria
uint8_t battery_buffer[sizeof(int)]; //Buffer para enviar el valor de la bateria por TCP

//Prototipos para algunas funciones
static void AskForPicture(void *arg);

//Para habilitar el debuggeo de la plataforma
#define testeo

/*!
 \fn size_t encodeCBOR(void)
 @brief Codifica las velocidades de la rueda en formato CBOR en un buffer.

 Inicializa el codificador CBOR con el buffer especificado y su tamaño, luego, se crea
 un array de CBOR con las velocidades de cada motor como un punto flotante. Por ultimo, 
 se cierra el contenedor del array y se devuelve el tamaño del buffer para ser enviado.

*/

size_t encodeCBOR(void)
{
    cbor_encoder_init(&encoder, cbor_buf_tx, sizeof(cbor_buf_tx), 0);
    cbor_encoder_create_array(&encoder, &array_encoder, 2);
    cbor_encode_float(&array_encoder, phi_ell);
    cbor_encode_float(&array_encoder, phi_r);
    cbor_encoder_close_container(&encoder, &array_encoder);

    return cbor_encoder_get_buffer_size(&encoder, cbor_buf_tx);
}

/*!
 \fn void UART_init(void)
 @brief Configura la interfaz UART.

 Configura los parametros del UART como la velocidad de transmision, tamaño del mensaje,
 paridad, bits de parada y el control de flujo entre transacciones. Se asignan los pines
 de TX y RX y se instala el controlador, inicializandolo para que opere en transacciones.
 
 \note El buffer de TX puede o no ser configurado, esto dependera del tamaño del mensaje.

*/

void UART_init(void)
{
    const uart_config_t uart_config = {
        .baud_rate = 115200,
        .data_bits = UART_DATA_8_BITS,
        .parity = UART_PARITY_DISABLE,
        .stop_bits = UART_STOP_BITS_1,
        .flow_ctrl = UART_HW_FLOWCTRL_DISABLE,
        .source_clk = UART_SCLK_APB
    };

    uart_driver_install(UART_PORT , RX_BUF_SIZE, 0, 0, NULL, 0);
    uart_param_config(UART_PORT , &uart_config);
    uart_set_pin(UART_PORT , TXD_PIN, RXD_PIN, UART_PIN_NO_CHANGE, UART_PIN_NO_CHANGE);   
}

/*!
 \fn static void wifi_event_handler(void* arg, esp_event_base_t event_base,int32_t event_id, void* event_data)
 @brief Handler del modulo WiFi.

 Despliega informacion sobre los eventos que ocurren luego de crear configurar el modulo WiFi y el Access Point,
 desplegando la direccion MAC e IP de los clientes al conectarse o desconectarse.
 
 \param event_base Define la variable utilizada para registrar el evento.
 \param event_id En este se indica el id del evento a registrar o si se deben de registrar todos los eventos.
 \param event_data Es la informacion de respuesta generada ante el evento registrado.
 \return En el monitor serial el estado de la conexion. 
 \note Este handler se utiliza en la funcion "esp__event_handler_instance_register", no debe de ser utilizado de
 manera directa en el codigo. 
*/

static void wifi_event_handler(void* arg, esp_event_base_t event_base,int32_t event_id, void* event_data)
{
    switch(event_id)
    {
        case WIFI_EVENT_AP_STACONNECTED:
        {
            wifi_event_ap_staconnected_t* event = (wifi_event_ap_staconnected_t*) event_data;
            ESP_LOGI(TAG, "station "MACSTR" join, AID=%d",MAC2STR(event->mac), event->aid);
            break;   
        }
        case WIFI_EVENT_AP_STADISCONNECTED:
        {
            wifi_event_ap_stadisconnected_t* event = (wifi_event_ap_stadisconnected_t*) event_data;
            ESP_LOGI(TAG, "station "MACSTR" leave, AID=%d",MAC2STR(event->mac), event->aid);
            break;
        }
        default:
            break;

    }
}

/*!
 \fn void wifi_init_softap(void)
 @brief Inicializa y configura el modulo WiFi como Access Point (SoftAP)

 Configura el modulo WiFi como un Access Point utilizando el nombre de red (SSID) y contraseña (WIFIPASSWORD),
 este se configura utilizando el protocolo de seguridad WPA2-PSK, manteniendo a la red segura. Al finalizar
 la configuracion despliega un mensaje con los parametros necesarios para la conexion a la red.
 
 \note Solo se debe de llamar una vez y esto luego de haber inicializado la NVS
 \see void nvs_init(void)

*/

void wifi_init_softap(void)
{
    ESP_ERROR_CHECK(esp_netif_init());
    ESP_ERROR_CHECK(esp_event_loop_create_default());
    esp_netif_create_default_wifi_ap();

    wifi_init_config_t cfg = WIFI_INIT_CONFIG_DEFAULT();
    ESP_ERROR_CHECK(esp_wifi_init(&cfg));

    ESP_ERROR_CHECK(esp_event_handler_instance_register(WIFI_EVENT,ESP_EVENT_ANY_ID,&wifi_event_handler,NULL,NULL));

    wifi_config_t wifi_config = {
        .ap = {
            .ssid = SSID,
            .ssid_len = strlen(SSID),
            .channel = WIFICHANNEL,
            .password = WIFIPASSWORD,
            .max_connection = MAXCONNECTIONS,
            .authmode = WIFI_AUTH_WPA2_PSK,
            .pmf_cfg = {
                    .required = true,
            },
        },
    };

    ESP_ERROR_CHECK(esp_wifi_set_mode(WIFI_MODE_AP));
    ESP_ERROR_CHECK(esp_wifi_set_config(WIFI_IF_AP, &wifi_config));
    ESP_ERROR_CHECK(esp_wifi_start());

    ESP_LOGI(TAG, "wifi_init_softap finished. SSID:%s password:%s channel:%d",SSID, WIFIPASSWORD, WIFICHANNEL);
}

/*!
 \fn void nvs_init(void)
 @brief Inicializa el sistema de almacenamiento flash no volatil (NVS).

 Inicializa el sistema de almacenamiento flash no volatil (NVS), verificando la cantidad de 
 paginas libres en la flash y la ultima version utilizada para su configuracion. Si no hay suficientes
 paginas libres o al momento de cargar el codigo hay una nueva version, borra la flash y la
 configura para poder ser utilizada por otros modulos. Por ultimo, despliega en el monitor serial
 los posibles errores que se presenten al configurarla.

*/

void nvs_init(void)
{
    esp_err_t ret = nvs_flash_init();
    if (ret == ESP_ERR_NVS_NO_FREE_PAGES || ret == ESP_ERR_NVS_NEW_VERSION_FOUND) 
    {
        ESP_ERROR_CHECK(nvs_flash_erase());
        ret = nvs_flash_init();
    }
    ESP_ERROR_CHECK(ret);  
}

/*!
 \fn static void TCPSendRobust(void *arg)
 @brief Envio de datos por medio del Socket TCP.

 Envia un paquete de gran tamaño por medio del socket WiFi al ser activada una bandera, 
 utilizando el tamaño del Buffer como referencia. Envia el paquete por porciones, 
 utilizando el ancho de banda maximo cuando es posible. En caso de presentarse un 
 error durante el envio lo despliega en el monito serial y al terminar el envio 
 exitosamente se baja la bandera.

*/

static void TCPSendRobust(void *arg)
{
    while(1)
    {

        if(tcpavail>0)
        {
            if (xSemaphore1 != NULL && xSemaphoreTake(xSemaphore1, (TickType_t)portMAX_DELAY) == pdTRUE){
                #ifdef testeo
                    printf ("TCPEnviado\n");
                #endif
                int to_write = BUFFER_SIZE;
                int written = 0;

                while (to_write > 0) {
                        written = send(sock, &rx_buffer, to_write, 0);
                    if (written < 0) {
                        #ifdef testeo
                            ESP_LOGE(TAG, "Error occurred during sending: errno %d", errno);
                        #endif
                        tcpavail = 0;
                    }
                    to_write -= written;
                }
                
                tcpavail = 0;
                xSemaphoreGive(xSemaphore1);
            }
        }

        vTaskDelay(10/ portTICK_PERIOD_MS);
    }
}

/*!
 \fn void handle_socket(void *pvParameters)
 @brief Handler para el manejo de los datos recibidos por WiFi.

 Utilizando el Socket creado para la conexion con el cliente, recibe un paquete de
 512 bytes utilizado en el handler. Con este paquete, toma la informacion del primer
 byte para determinar el tipo de tarea a realizar y como procesar el resto de bytes,
 ademas de cuales banderas activar para el proceso. En caso de recibir un paquete para 
 terminar la conexion, cierra el cliente y elimina la tarea creada.

 \param pvParameters Socket creado para la conexion con el cliente.

 \note Esta se utiliza como una tarea creada luego de terminar de configurar el Socket,
        para evitar errores de ejecucion.
*/
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
void app_main(void)
{   
    //Inicializar los semaphores de control
    initSemaphores();

    //Inicializando el UART
    UART_init();

    //Configurando el pin para encender el Pololu3pi+
    gpio_config_t pololuPin={
        .intr_type=GPIO_INTR_DISABLE,
        .mode=GPIO_MODE_OUTPUT,
        .pin_bit_mask=(1<<POLOLUSWITCH)
    };

    gpio_config(&pololuPin);
    
    //Configurando el MCPWM para manejar los servos y colocandolos en reposo
    mcpwm_initialize();
    configj1 = 90;
    configj2 = 90;
    configj3 = 160;
    vTaskDelay(1000 / portTICK_PERIOD_MS); //Seguridad, evita que los servomotores salten.
    
    //Configuracion del ADC
    ADCConfig();

    //Configurando el SPI
    SPI_init_config();
    //Inicializando el NVS
    nvs_init();
    //Inicializando el WIFI
    wifi_init_softap();

    //Nucleo principal
    xTaskCreatePinnedToCore(uart_tx, "uart_tx_task", 1024*2, NULL, configMAX_PRIORITIES - 1, NULL, 0); // Tarea en el núcleo 0
    xTaskCreatePinnedToCore(uart_rx, "uart_rx_task", 1024*2, NULL, configMAX_PRIORITIES - 1, NULL, 0); // Tarea en el núcleo 0
    xTaskCreatePinnedToCore(tcp_socket_init, "TCPSocket", 4096, NULL, configMAX_PRIORITIES - 2, NULL, 0); // Tarea en el núcleo 0
    //Nucleo secundario
    xTaskCreatePinnedToCore(AskForPicture, "SPIRetrieve", 4096, NULL, configMAX_PRIORITIES - 1, NULL, 1); // Tarea en el núcleo 1
    xTaskCreatePinnedToCore(updatePositionSCH, "MOVServo", 1024, NULL, configMAX_PRIORITIES - 1, NULL, 1); // Tarea en el núcleo 1
    xTaskCreatePinnedToCore(CalcConfig, "CalcPosition", 1024, NULL, configMAX_PRIORITIES - 2, NULL, 1); // Tarea en el núcleo 1
    xTaskCreatePinnedToCore(BatteryUpadte, "UpdateBateria", 1024, NULL, configMAX_PRIORITIES - 1, NULL, 1); // Tarea en el núcleo 1

}

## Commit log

2023-06-14 Pruebas TCP-IP
    Pruebas de comunicacion utilizando el stack TCP-IP con lwIP, envio de datos sencillos
2023-06-15 Echo TCP-IP
    Se coloco el Echo TCP-IP para las pruebas, se determino el tamaño mas grande del paquete para su envio y una manera robusta de enviarlo porr paquetes.
2023-06-16 Robustes en la comunicacion
2023-07-10 Pruebas en Python
    Pruebas en Python para el envio de jpeg en vez de la imagen directa, cambiando el modo de activar la bandera para el envio.
2023-07-10 Prueba LEDC
    Prueba de configuracion y funcionamiento del LEDC
2023-07-10 Prueba multiples servos
    Prueba de multiples canales con el modulo LEDC para el control de distintos servos a distintos ciclos de trabajo
2023-07-10 mapeo de angulo a ciclo de trabajo
    agregado el mapeo de valores de angulo a ciclo de trabajo para el control de los servomotores
2023-07-15 cambio tamaño de mensajes
    Modificacion para el envio de mensajes variables.
2023-07-16 Implementacion SPI
    Implementacion del SPI para el envio y recepcion de datos con la OpenMV Cam H7
2023-07-17 Arreglado recepcion SPI
    Se arreglo la recepcion de datos de SPI, implementando el determinar la cantidad de datos a recibir.
    [main.c]
2023-07-18 Envio de JPEG
    Implementado el servidor WiFi para el envio de la imagen codificada como JPEG. Solamente envia una imagen y se apaga el servidor.
2023-07-21 Arreglo del Socket TCP
    Comunicacion SPI robusta, comenzando el arreglo del Socket para evitar el reinicio del ESP luego de la desconexion.
    [main.c]
2023-07-23 Resuelto el reinicio
    Se resolvio el reinicio luego del envio de cada dato por el Socket, no envia los datos correctos
    [main.c]
2023-07-24 Socket arreglado
    Envio del fotograma en formato JPG terminado. Continua la implementacion de un metodo para evitar la perdida de informacion.
    [main.c]
2023-08-05 Limpieza de codigo
    Se limpio el codigo y se comienza con la recepcion de distintas instrucciones por meido de Wifi
2023-08-06 Control de servomotores
    Contro de servomotores de manera bloqueante al enviar la configuracion de cada junta por medio de wifi
2023-08-08 Control de servos e imagen arreglado
    Se volvio al envio de imagen en bruto por estabilidad. Se controlan los servos por medio de un mensaje en wifi y todo funciona en conjunto
    [main.c]
2023-08-24 nuevas features
    Se agrego la capacidad para encender y apagar el resto de modulos.
    Se esta comenzando a integrar la capacidad para mover el brazo a una coordenada especifica.
2023-08-25 Proteccion de movimiento
    Implementados limites de configuracion de los servomotores para evitar colisiones fisicas en movimiento
2023-09-22 Adicion del ADC
    Se agrego el modulo y lectura del ADC en modo oneshot, para detectar el nivel de la bateria cada segundo.
2023-09-22 Terminado ADC/Estructura recepcion.
    Se termino la adicion del ADC a la placa, ya se obtienen los valores por peticion WiFi. Ahora se implemento el paquete para el envio de datos.
2023-09-27 Video agregado
    Agregado el video de las primeras iteraciones del agente estacionandose.
2023-10-14 Inicio doxygen
    Se inicio la documentacion utilizando Doxygen.
2023-10-20 recepcion flotantes de velocidad
    Se recibe los valores flotantes como velocidad.
2023-10-29 Implementacion de UART con el agente
    Se implemento CBOR para la comunicacion con el agente por medio de UART.
2023-11-11 Cambios calendarizacion
    Se cambio el orden para calendarizar las tareas e idealizar mejor el envio de datos y estructuras.
2023-11-19 Modificaciones en envio
    Se modifico la estructura de control para el envio de datos, para reducir los errores al usar la odometria interna y el envio de imagenes al mismo tiempo.
    [main.c]
2023-11-23 Actualizacion de la documentacion
    Se actualiza la documentacion de los archivos.
2023-11-24 archivos de manufactura
    [BaseBrazoV1.stl, BaseGarra-01.stl, BaseGarra-02.stl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]
2023-11-24 Control desde Python
    Funciones de control para el agente, conectandose como cliente desde python
2023-11-25 Limpieza del codigo
    Se limpio el codigo y termino de comentar para la entrega final del proyecto.
